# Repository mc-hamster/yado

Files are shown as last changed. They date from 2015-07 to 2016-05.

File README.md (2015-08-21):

# yado (Pronounced Yah-Dew)
"Yet Another Door Opener" ... ESP8266 based Door Controller with JSON REST API and Secure Password ACL. Intened for Garage Doors and Electronic Gate "Buzzers".

## Features

1. Open hardware available in ./hardware
 1. PCB available for purchase at OSHPark
  1. https://www.oshpark.com/shared_projects/0cBHd21f
 2. Full BOM available with distributor list.
  1. (See BOM in ./hardware for part list)
 3. Utilizes nodemcu dev board (It includes many components and just $7 on ebay)
 4. Supports both v0.9 and v1.0 nodemcu footprints. 
   1. http://www.aliexpress.com/wholesale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
1. Open source code available in ./src.
2. Completed Features:
 1. Digest based authentication (No clear text passwords) ... Done
 2. Support for DHCP & Static addresses ... Done
 3. JSON REST API to read door sensors ... Done
 4. Serve all javascript libaries locally ... Done
3. In progress
 1. JSON REST API
  1. Open/Close door ... In progress
  2. Contact Sensor status ... Done
  3. New server digest and payload ... Done
 2. Web Admin Interface for configuration ... In progress
  1. Captive portal ... Done
   1.. Note: DNS server library is unreliable. May cause ESP8266 watchdog reset.

## JSON REST

1. /json/sensors
 1. Return state of the sensors
2. /json/digest/new
 1. Generate a new server digest and associated time

## To build code

1. Install Arduino IDE (It's a horrible environment, but easiest to get going): http://arduino.cc
2. Install board support for the ESP8266: https://github.com/esp8266/Arduino
 1. Select your NodeMCU from the board menu.
3. Install  USB to TTL Bridge Drivers
 1. CH341 : http://www.electrodragon.com/w/CH341 (older nodemcu)
 2. CP2102 : Mac - Drivers built in. Windows - Use windows update. (newer nodemcu)
4. Load the Yagdo code into the Arduino IDE
5. Compile and load the code into your nodemcu dev board.

### Optional

1. Install Atmel Studio and Visual Micro. This is a better IDE than the Arduino IDE.

## Usage: Admin interface

1. Provide power to Yado
2. The LED1 will light solid for a few seconds. During this period, hold down the "user_flash" button.
3. Onces you press the button, LED1 will turn off.
4. When LED2 blinks. Let go of "user_flash".
5. Connect to the Yado access point.
 1. SSID: yado_admin
 2. Password: yado_admin
6. Point your browser to http://192.168.4.1
7. If this is your first time, select the "Load Defaults" link from main menu.

LED2 will continue to blink while Yado is in admin mode. Because unsecured networks are a bad idea, we have conciously decided not to support unsecured Access Points and they won't be listed in the WiFi configuration. Adding support will be a 3 line change, but let's not do it.

Using static IP addresses is recommended, but DHCP also works. The assigned DHCP address is available through the USB serial console (115200, 8n1) on startup, through your home router's interface or you can scan the network for Yado.

Important Note: You will have 30 minutes to make your changes. After 30 minutes, Yado will return to the default operation.

## Usage: Normal Interface

1. Point your web browser to Yado's IP address.
2. Type your access password and click 'open'.

## Usage: Installation

1. Connect the terminal labled "Open1" to your garage door opener.
2. Install an optional door sensor to "Sens1" or "Sens2".

Open2 is not used. Adding support it will some (very) minimal effort, but the UI will need to be kept simple.

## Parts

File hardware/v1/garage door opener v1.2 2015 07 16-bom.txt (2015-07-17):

Partlist exported from /Users/jmcasler/Documents/CloudStation/projects/yado/hardware/garage door opener v2 2015 07 16.sch at 7/17/15 12:47 AM

Part    Value       Device                    Package   Description                MF     MPN         OC_FARNELL OC_NEWARK
C1      10uf        C-USC0603                 C0603     CAPACITOR, American symbol                                        
C2      10uf        C-USC0603                 C0603     CAPACITOR, American symbol                                        
D1      1N4004      DIODE-DO214BA             DO214BA   DIODE                                                             
D2      1N4004      DIODE-DO214BA             DO214BA   DIODE                                                             
D3                  LED0603                   LED-0603  LEDs                                                              
D4                  LED0603                   LED-0603  LEDs                                                              
DS18B20 DS18B20TO92 DS1820TO92                DS1820    DS18B20                                                           
JP1                 PINHD-1X15                1X15      PIN HEADER                                                        
JP2                 PINHD-1X15                1X15      PIN HEADER                                                        
JP3                 PINHD-1X15                1X15      PIN HEADER                                                        
K1      HE3621      HE3621                    HE3621    RELAY                      HAMLIN HE3621A0510 9561943    50F7993  
K2      HE3621      HE3621                    HE3621    RELAY                      HAMLIN HE3621A0510 9561943    50F7993  
OPEN1   1X2-3.5MM   1X2-3.5MM                 1X2-3.5MM 3.5mm Terminal block              OSTTE020161                     
OPEN2   1X2-3.5MM   1X2-3.5MM                 1X2-3.5MM 3.5mm Terminal block              OSTTE020161                     
R1      42          R-US_R0603                R0603     RESISTOR, American symbol                                         
R2      3.3k        R-US_R0603                R0603     RESISTOR, American symbol                                         
R3      42          R-US_R0603                R0603     RESISTOR, American symbol                                         
R4      3.3k        R-US_R0603                R0603     RESISTOR, American symbol                                         
R5      3.3k        R-US_R0603                R0603     RESISTOR, American symbol                                         
R6      3.3k        R-US_R0603                R0603     RESISTOR, American symbol                                         
R7      3.3k        R-US_R0603                R0603     RESISTOR, American symbol                                         
R8      3.3k        R-US_R0603                R0603     RESISTOR, American symbol                                         
R9      3.3k        R-US_R0603                R0603     RESISTOR, American symbol                                         
SENS1   1X2-3.5MM   1X2-3.5MM                 1X2-3.5MM 3.5mm Terminal block              OSTTE020161                     
SENS2   1X2-3.5MM   1X2-3.5MM                 1X2-3.5MM 3.5mm Terminal block              OSTTE020161                     
T1                  MMBT3904LT1-NPN-SOT23-BEC SOT23-BEC NPN Transistror                   MMBT2222A                       
T2                  MMBT3904LT1-NPN-SOT23-BEC SOT23-BEC NPN Transistror                   MMBT2222A

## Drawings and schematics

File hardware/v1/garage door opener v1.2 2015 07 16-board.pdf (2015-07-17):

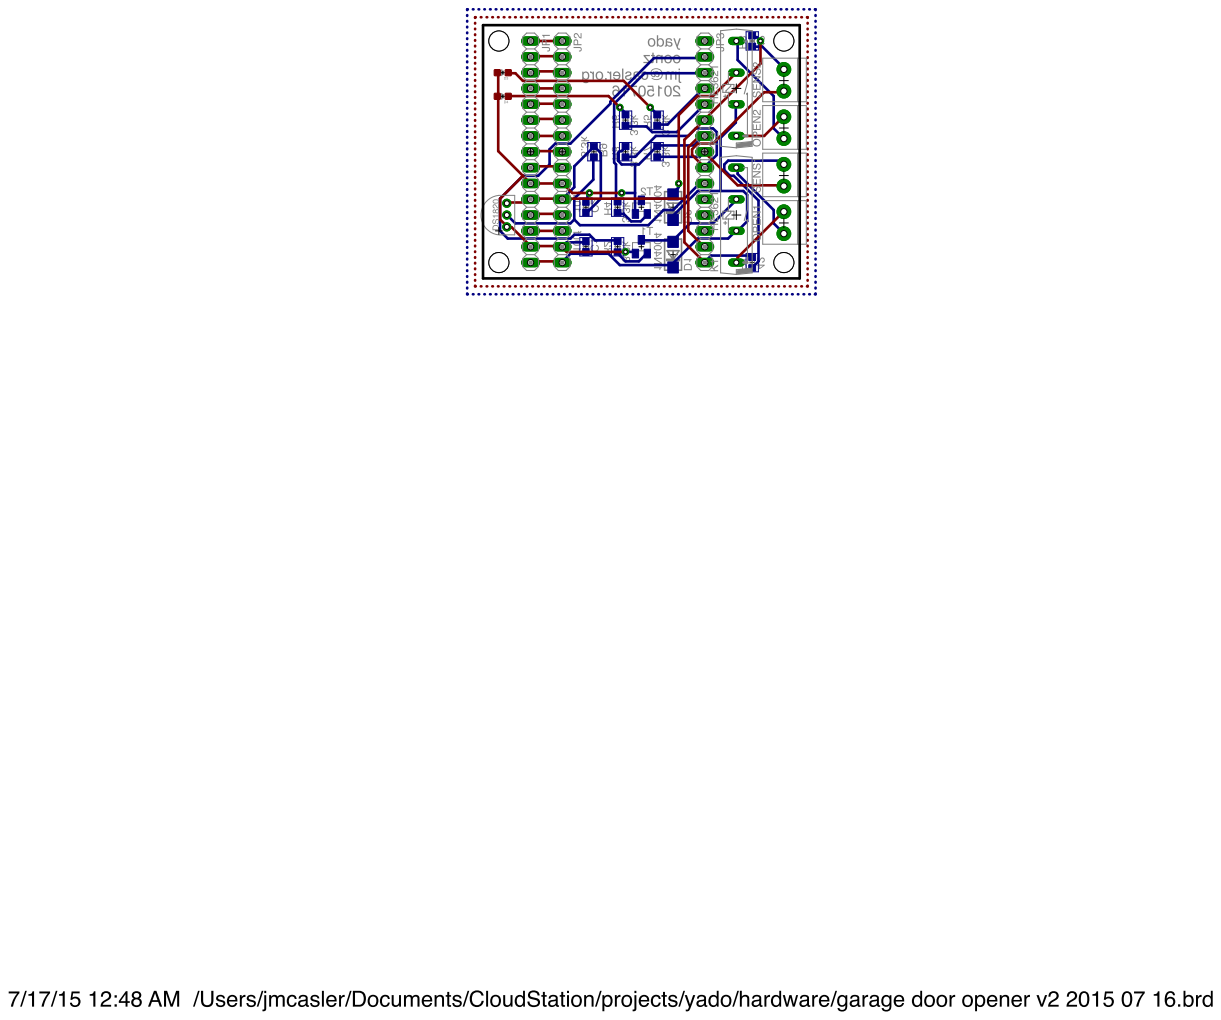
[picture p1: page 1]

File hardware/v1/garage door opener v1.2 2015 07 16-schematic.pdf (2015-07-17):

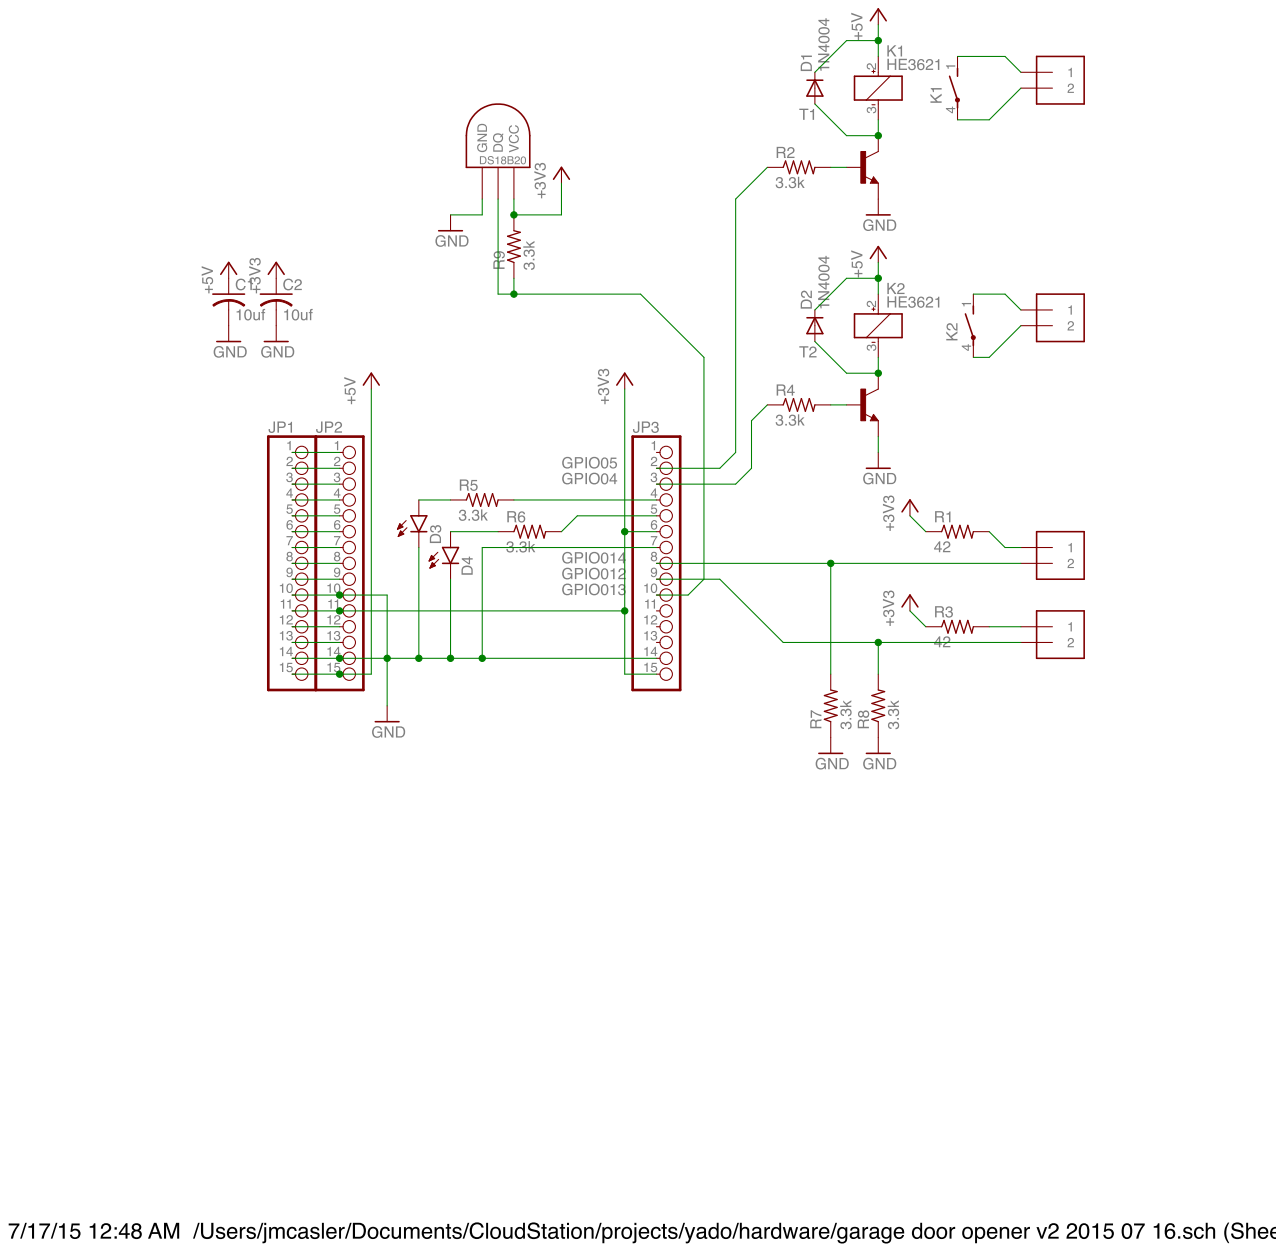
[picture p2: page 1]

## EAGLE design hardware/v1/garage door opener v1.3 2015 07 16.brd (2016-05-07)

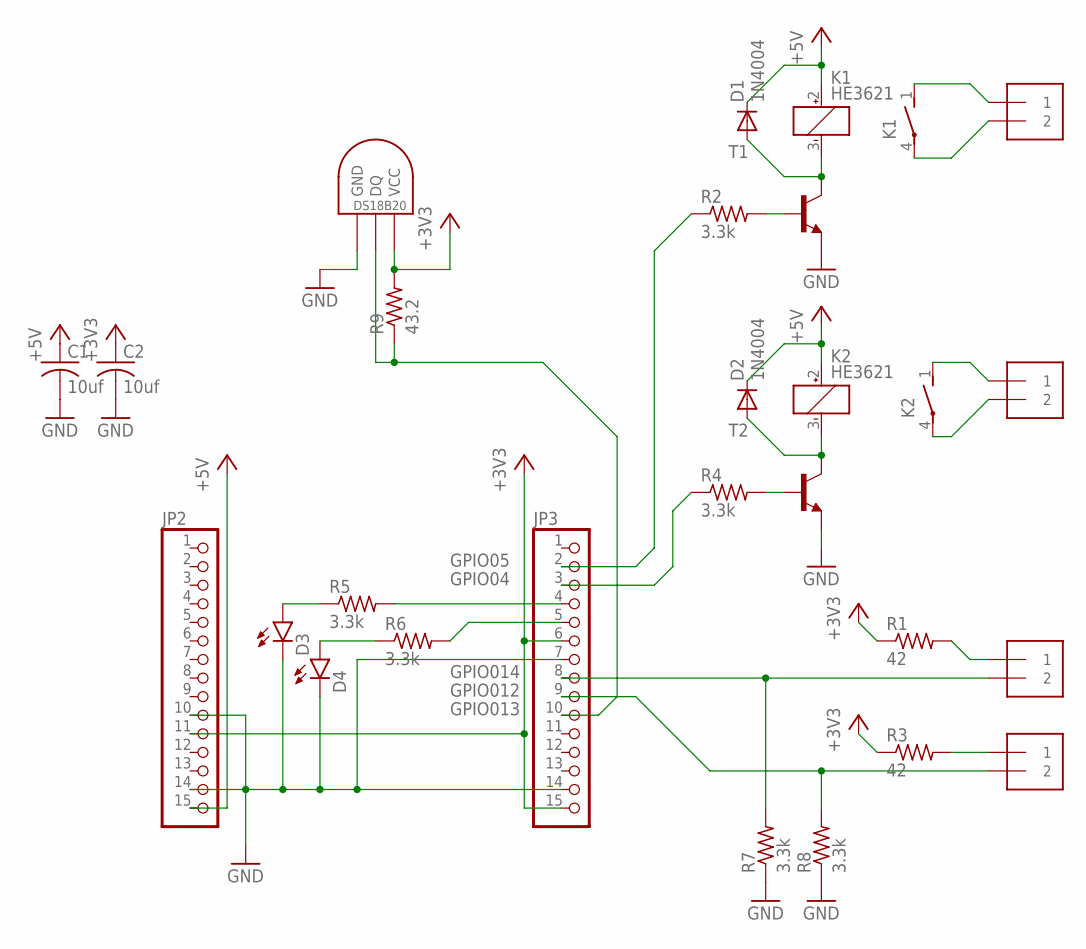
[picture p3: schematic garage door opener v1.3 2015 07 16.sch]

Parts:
C1, C2: 10uf; C0603
D1, D2: 1N4004; DO214BA
D3, D4: LED0603; LED-0603
DS18B20: DS18B20TO92; DS1820
JP2, JP3: PINHD-1X15; 1X15
K1, K2: HE3621; MPN HE3621A0510
OPEN1, OPEN2: 1X2-3.5MM; MPN OSTTE020161
R1, R3: 42; R0603
R2, R4, R5, R6, R7, R8: 3.3k; R0603
R9: 43.2; R0603
SENS1, SENS2: 1X2-3.5MM; MPN OSTTE020161
T1, T2: MMBT3904LT1-NPN-SOT23-BEC; SOT23-BEC; MPN MMBT2222A

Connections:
+3V3: C2.1, DS18B20.VDD (VCC), JP2.11, JP3.6, JP3.15, R1.1, R3.1, R9.2
+5V: C1.1, D1.C, D2.C, JP2.15, K1.2 (+), K2.2 (+)
GND: C1.2, C2.2, D3.C, D4.C, DS18B20.GND, JP2.10, JP2.14, JP3.7, JP3.14, R7.1, R8.1, T1.E, T2.E
unnamed: K1.1 (S), OPEN1.1
unnamed: K1.4, OPEN1.2
unnamed: JP3.8, R7.2, SENS1.2
unnamed: R1.2, SENS1.1
unnamed: D1.A, K1.3 (-), T1.C
unnamed: JP3.2, R2.1
unnamed: R2.2, T1.B
unnamed: JP3.4, R5.2
unnamed: JP3.5, R6.2
unnamed: R3.2, SENS2.1
unnamed: JP3.9, R8.2, SENS2.2
unnamed: K2.1 (S), OPEN2.1
unnamed: K2.4, OPEN2.2
unnamed: D2.A, K2.3 (-), T2.C
unnamed: JP3.3, R4.1
unnamed: R4.2, T2.B
unnamed: D4.A, R6.1
unnamed: D3.A, R5.1
unnamed: DS18B20.DQ, JP3.10, R9.1

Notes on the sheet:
GPIO05
GPIO04
GPIO014
GPIO012
GPIO013

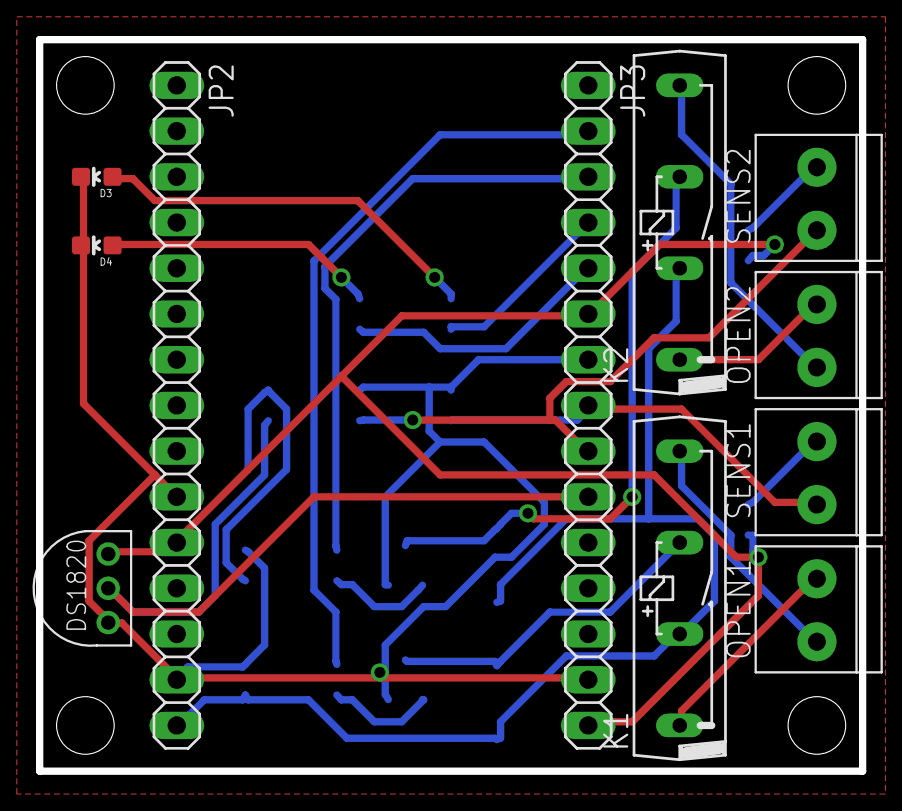
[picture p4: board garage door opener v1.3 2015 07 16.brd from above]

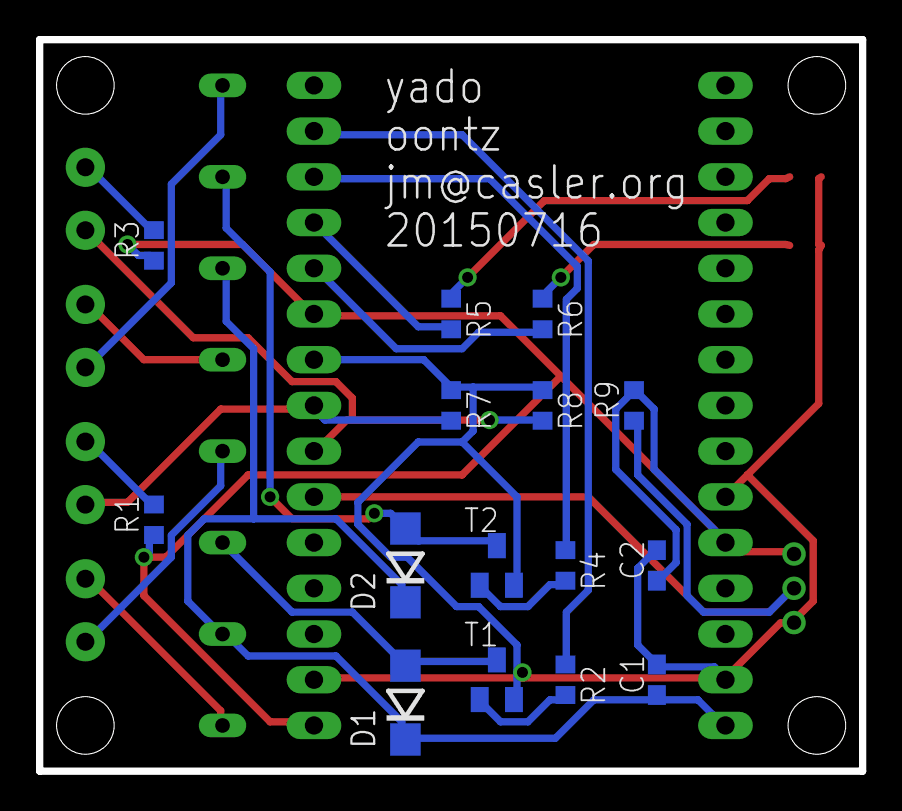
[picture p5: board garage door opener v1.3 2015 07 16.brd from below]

Board: 2 copper layers, 45.7 x 40.6 mm, 26 parts (15 on the bottom side), 22 nets.

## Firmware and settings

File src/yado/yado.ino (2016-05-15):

/*
 * Copyright (c) 2015-2016, Jm Casler
 * All rights reserved.
 *
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
 * * Neither the name of Jm Casler nor the names of its
 *   contributors may be used to endorse or promote products derived from
 *   this software without specific prior written permission.
 *
 * THIS SOFTWARE IS PROVIDED BY THE COPYRIGHT HOLDERS AND CONTRIBUTORS "AS IS" AND
 * ANY EXPRESS OR IMPLIED WARRANTIES, INCLUDING, BUT NOT LIMITED TO, THE IMPLIED
 * WARRANTIES OF MERCHANTABILITY AND FITNESS FOR A PARTICULAR PURPOSE ARE
 * DISCLAIMED. IN NO EVENT SHALL THE COPYRIGHT HOLDER OR CONTRIBUTORS BE LIABLE FOR
 * ANY DIRECT, INDIRECT, INCIDENTAL, SPECIAL, EXEMPLARY, OR CONSEQUENTIAL DAMAGES
 * (INCLUDING, BUT NOT LIMITED TO, PROCUREMENT OF SUBSTITUTE GOODS OR SERVICES;
 * LOSS OF USE, DATA, OR PROFITS; OR BUSINESS INTERRUPTION) HOWEVER CAUSED AND ON
 * ANY THEORY OF LIABILITY, WHETHER IN CONTRACT, STRICT LIABILITY, OR TORT
 * (INCLUDING NEGLIGENCE OR OTHERWISE) ARISING IN ANY WAY OUT OF THE USE OF THIS
 * SOFTWARE, EVEN IF ADVISED OF THE POSSIBILITY OF SUCH DAMAGE.
 */

#include <ESP8266WiFi.h>
#include <DNSServer.h>
#include <WiFiClient.h>
#include <ESP8266WebServer.h>
#include <Hash.h>

#include <EEPROM.h>
#include "EEPROMAnything.h"

#include <ESP8266HTTPUpdateServer.h>
#include <ESP8266mDNS.h>


// Configuration Start
const uint8_t numberOfUsers = 5;
const uint8_t passwordLength = 16;
const uint8_t noteLength = 32;

const uint8_t sensorLabelLength = 16;

const char* host = "yado";

// Contact sensors
struct sensor_t
{
  boolean enabled;
  boolean invert;
  char name[sensorLabelLength + 1]; // One more byte than required; String needs to be null terminated
  char high[sensorLabelLength + 1];  // One more byte than required; String needs to be null terminated
  char low[sensorLabelLength + 1];  // One more byte than required; String needs to be null terminated
};

struct temperature_t
{
  boolean enabled;
  boolean metricImperial; // 0 = Metric, 1 = Imperial
};

//
struct access_t
{
  uint8_t admin;  // Reserved
  uint8_t conf;   // Reserved
  char password[passwordLength + 1]; // One more byte than required; String needs to be null terminated
  char user[passwordLength + 1];  // Not yet used.
  char note[noteLength + 1];  // One more byte than required; String needs to be null terminated
};

// This structure should not grow larger than 1024 bytes.
struct settings_t
{
  uint8_t initialized;       // If not "1", then we have not yet initialized with defaults
  char ssid[33];         // One more byte than required; String needs to be null terminated
  char ssidPassword[65]; // One more byte than required; String needs to be null terminated
  uint8_t ipMode; // 0 = Dynamic, 1 = Static
  uint8_t ipAddress[4]; // 255.255.255.255
  uint8_t ipGateway[4]; // 255.255.255.255
  uint8_t ipSubnet[4];  // 255.255.255.255
  access_t accessGeneral[numberOfUsers];
  sensor_t contactSensor[2];
  temperature_t temperature;
} settings;

int requestTTL = 120;


// Configuration End

const byte DNS_PORT = 53;
ESP8266WebServer httpServer ( 80 );
ESP8266HTTPUpdateServer httpUpdater;
DNSServer dnsServer;

// Pin Assignment
const int ledHTTP = 0;     // Toggled on HTTP Status
const int ledCONNECTED = 2; // Toggled on when AP connected
const int sensor1 = 14;
const int sensor2 = 12;
const int open1 = 5;
const int open2 = 4;

// These buttons are exposed on the nodemcu dev board
const int key_user = 16; // What can we do with this button?
const int key_flash = 0; // If pressed within 5 seconds of power on, enter admin mode
// End Pin Assignment

unsigned long secretRandNumber; // We will generate a new secret on startup.

int lastAccessTime = 0;

String inputString = "";         // a string to hold incoming data

boolean deviceAdmin = 0;

// Define the LED state for ledHTTP
//   This is used for blinking the LED with a non-blocking method
boolean ledHTTPState = LOW;
unsigned long    ledHTTPStateMills = 0;
long    ledHTTPStateInterval = 250; // How fast to blink the LED



void setup ( void ) {
  EEPROM.begin(1024); // 512 bytes should be more than enough (famous last words)
  loadSettings();

  // TODO: Move this into the admin setup menu.
  settings.contactSensor[0].enabled = 1; // Manually enable this for now.
  settings.contactSensor[0].invert = 9; // Manually enable this for now.


  inputString.reserve(50);

  // Set relays as outputs;
  pinMode ( open1, OUTPUT );
  pinMode ( open2, OUTPUT );
  digitalWrite ( open1, 0 );
  digitalWrite ( open2, 0 );


  //  There is a bug in the esp8266 library which prevents the pulldown from functioning
  //    https://github.com/esp8266/Arduino/issues/478
  pinMode ( sensor1, INPUT );
  pinMode ( sensor2, INPUT );

  // Set status LEDs to OUTPUT
  pinMode ( ledHTTP, OUTPUT );
  pinMode ( ledCONNECTED, OUTPUT );
  digitalWrite ( ledHTTP, 0 );
  digitalWrite ( ledCONNECTED, 0 );

  // Get access to the key_user button
  pinMode( key_flash, INPUT_PULLUP );


  delay(5000);
  // Set deviceAdmin to one if key_flash is depressed. Otherwise, use defaults.
  if (digitalRead( key_flash ) == 0) {
    deviceAdmin = 1;
    pinMode( key_flash, OUTPUT );
  } else {
    pinMode( key_flash, OUTPUT );
  }

  Serial.begin ( 115200 );

  if (deviceAdmin) {
    WiFi.mode(WIFI_AP);
    WiFi.softAP("yado_admin", "yado_admin");
    //WiFi.mode(WIFI_AP);
    WiFi.config ( IPAddress(192, 168, 4, 1), IPAddress(192, 168, 4, 1), IPAddress(255, 255, 255, 0)) ;
    delay(10);

    // if DNSServer is started with "*" for domain name, it will reply with
    // provided IP to all DNS request
    dnsServer.start(DNS_PORT, "*", IPAddress(192, 168, 4, 1));

    //WiFi.printDiag(Serial);
    Serial.println ( "Entering admin mode." );

    Serial.print ( "IP address: " );
    Serial.println ( WiFi.softAPIP() );
    printAPMacAddress();


    if ( MDNS.begin ( host ) ) {
      Serial.println ( "MDNS responder started" );
    } else {
      Serial.println ( "MDNS responder NOT started" );
    }

    // We are using the amount of time required to connect to the AP as the seed to a random number generator.
    //   We should look for other ways to improve the seed. This should be "good enough" for now.

    httpServer.on ( "/", handleAdminFrameset );
    httpServer.on ( "/leftnav", handleAdminNav );
    httpServer.on ( "/conf/wifi", handleAdminConfWifi );
    httpServer.on ( "/conf/network", handleAdminConfNetwork );
    httpServer.on ( "/conf/accounts", handleAdminConfAccounts );
    httpServer.on ( "/conf/sensors", handleAdminConfSensors );
    httpServer.on ( "/system/defaults", handleAdminDefaults );
    httpServer.on ( "/system/settings", handleAdminSettings );
    httpServer.on ( "/system/restart", handleAdminRestart);
    httpServer.on ( "/system/apply", handleAdminApply);
    httpServer.on ( "/yado.css", handleCSS);

    httpServer.onNotFound ( handleNotFound );

    httpUpdater.setup(&httpServer); // Handle OTA Updates. Go to http://yado.local/update

    httpServer.begin();
    Serial.println ( "HTTP server started" );

    MDNS.addService("http", "tcp", 80);
    Serial.printf("HTTPServer ready! Open http://%s.local in your browser\n", host);
    Serial.printf("HTTPUpdateServer ready! Open http://%s.local/update in your browser\n", host);


  } else {
    WiFi.begin ( settings.ssid, settings.ssidPassword );
    WiFi.mode ( WIFI_STA );



    // Documentation says this is supposed to come before WiFi.begin, but when it is there -- it doesn't work. WHY?!?!?!
    if (settings.ipMode == 1) { // 0 = Dynamic, 1 = Static
      WiFi.config ( settings.ipAddress, settings.ipGateway, settings.ipSubnet) ;
    }

    Serial.println ( "" );

    //EEPROM_readAnything(0, settings);

    // Wait for connection
    while ( WiFi.status() != WL_CONNECTED ) {
      delay ( 500 );
      Serial.print ( "." );
    }

    digitalWrite ( ledCONNECTED, 1 );

    WiFi.printDiag(Serial);

    Serial.print ( "IP address: " );
    Serial.println ( WiFi.localIP() );
    printMacAddress();

    if ( MDNS.begin ( host ) ) {
      Serial.println ( "MDNS responder started" );
    } else {
      Serial.println ( "MDNS responder NOT started" );
    }

    // We are using the amount of time required to connect to the AP as the seed to a random number generator.
    //   We should look for other ways to improve the seed. This should be "good enough" for now.
    randomSeed(micros());
    secretRandNumber = random(2147483646); // Full range of long 2147483647
    Serial.println("Secret: " + String(secretRandNumber));

    httpServer.on ( "/", handleRoot );
    httpServer.on ( "/externalScript.js", handleExternalScriptJS );
    httpServer.on ( "/json/sensors", handleJSONSensors );
    httpServer.on ( "/json/digest/new", handleJSONDigestNew );
    httpServer.on ( "/yado.css", handleCSS);

    httpServer.onNotFound ( handleNotFound );
    httpServer.begin();
    Serial.println ( "HTTP server started" );

    MDNS.addService("http", "tcp", 80);
    Serial.printf("HTTP Server ready! Open http://%s.local in your browser\n", host);

  
  }

}


void loop ( void ) {

  httpServer.handleClient();
  dnsServer.processNextRequest();

  if (deviceAdmin) {
    unsigned long ledHTTPCurrentMills = millis();

    if (ledHTTPCurrentMills - ledHTTPStateMills > ledHTTPStateInterval) {
      ledHTTPStateMills = ledHTTPCurrentMills;

      if (ledHTTPState) {
        ledHTTPState = 0;
      } else {
        ledHTTPState = 1;
      }
      digitalWrite( ledCONNECTED, ledHTTPState );
      //Serial.println ( WiFi.softAPIP() );
    }

    // If we've been in admin mode for 30 minutes, reboot ESP to get out of
    //   admin mode.
    if (millis() > 1800000) {
      ESP.reset();
    }
  }

}

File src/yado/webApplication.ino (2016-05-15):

void handleExternalScriptJS() {
  digitalWrite ( ledHTTP, 1 );


  String externJavascriptString = "\n"
                                  "/*CryptoJS v3.1.2\n"
                                  "code.google.com/p/crypto-js\n"
                                  "(c) 2009-2013 by Jeff Mott. All rights reserved.\n"
                                  "code.google.com/p/crypto-js/wiki/License\n"
                                  "*/\n"
                                  "var CryptoJS=CryptoJS||function(e,m){var p={},j=p.lib={},l=function(){},f=j.Base={extend:function(a){l.prototype=this;var c=new l;a&&c.mixIn(a);c.hasOwnProperty(\"init\")||(c.init=function(){c.$super.init.apply(this,arguments)});c.init.prototype=c;c.$super=this;return c},create:function(){var a=this.extend();a.init.apply(a,arguments);return a},init:function(){},mixIn:function(a){for(var c in a)a.hasOwnProperty(c)&&(this[c]=a[c]);a.hasOwnProperty(\"toString\")&&(this.toString=a.toString)},clone:function(){return this.init.prototype.extend(this)}},\n"
                                  "n=j.WordArray=f.extend({init:function(a,c){a=this.words=a||[];this.sigBytes=c!=m?c:4*a.length},toString:function(a){return(a||h).stringify(this)},concat:function(a){var c=this.words,q=a.words,d=this.sigBytes;a=a.sigBytes;this.clamp();if(d%4)for(var b=0;b<a;b++)c[d+b>>>2]|=(q[b>>>2]>>>24-8*(b%4)&255)<<24-8*((d+b)%4);else if(65535<q.length)for(b=0;b<a;b+=4)c[d+b>>>2]=q[b>>>2];else c.push.apply(c,q);this.sigBytes+=a;return this},clamp:function(){var a=this.words,c=this.sigBytes;a[c>>>2]&=4294967295<<\n"
                                  "32-8*(c%4);a.length=e.ceil(c/4)},clone:function(){var a=f.clone.call(this);a.words=this.words.slice(0);return a},random:function(a){for(var c=[],b=0;b<a;b+=4)c.push(4294967296*e.random()|0);return new n.init(c,a)}}),b=p.enc={},h=b.Hex={stringify:function(a){var c=a.words;a=a.sigBytes;for(var b=[],d=0;d<a;d++){var f=c[d>>>2]>>>24-8*(d%4)&255;b.push((f>>>4).toString(16));b.push((f&15).toString(16))}return b.join(\"\")},parse:function(a){for(var c=a.length,b=[],d=0;d<c;d+=2)b[d>>>3]|=parseInt(a.substr(d,\n"
                                  "2),16)<<24-4*(d%8);return new n.init(b,c/2)}},g=b.Latin1={stringify:function(a){var c=a.words;a=a.sigBytes;for(var b=[],d=0;d<a;d++)b.push(String.fromCharCode(c[d>>>2]>>>24-8*(d%4)&255));return b.join(\"\")},parse:function(a){for(var c=a.length,b=[],d=0;d<c;d++)b[d>>>2]|=(a.charCodeAt(d)&255)<<24-8*(d%4);return new n.init(b,c)}},r=b.Utf8={stringify:function(a){try{return decodeURIComponent(escape(g.stringify(a)))}catch(c){throw Error(\"Malformed UTF-8 data\");}},parse:function(a){return g.parse(unescape(encodeURIComponent(a)))}},\n"
                                  "k=j.BufferedBlockAlgorithm=f.extend({reset:function(){this._data=new n.init;this._nDataBytes=0},_append:function(a){\"string\"==typeof a&&(a=r.parse(a));this._data.concat(a);this._nDataBytes+=a.sigBytes},_process:function(a){var c=this._data,b=c.words,d=c.sigBytes,f=this.blockSize,h=d/(4*f),h=a?e.ceil(h):e.max((h|0)-this._minBufferSize,0);a=h*f;d=e.min(4*a,d);if(a){for(var g=0;g<a;g+=f)this._doProcessBlock(b,g);g=b.splice(0,a);c.sigBytes-=d}return new n.init(g,d)},clone:function(){var a=f.clone.call(this);\n"
                                  "a._data=this._data.clone();return a},_minBufferSize:0});j.Hasher=k.extend({cfg:f.extend(),init:function(a){this.cfg=this.cfg.extend(a);this.reset()},reset:function(){k.reset.call(this);this._doReset()},update:function(a){this._append(a);this._process();return this},finalize:function(a){a&&this._append(a);return this._doFinalize()},blockSize:16,_createHelper:function(a){return function(c,b){return(new a.init(b)).finalize(c)}},_createHmacHelper:function(a){return function(b,f){return(new s.HMAC.init(a,\n"
                                  "f)).finalize(b)}}});var s=p.algo={};return p}(Math);\n"
                                  "(function(){var e=CryptoJS,m=e.lib,p=m.WordArray,j=m.Hasher,l=[],m=e.algo.SHA1=j.extend({_doReset:function(){this._hash=new p.init([1732584193,4023233417,2562383102,271733878,3285377520])},_doProcessBlock:function(f,n){for(var b=this._hash.words,h=b[0],g=b[1],e=b[2],k=b[3],j=b[4],a=0;80>a;a++){if(16>a)l[a]=f[n+a]|0;else{var c=l[a-3]^l[a-8]^l[a-14]^l[a-16];l[a]=c<<1|c>>>31}c=(h<<5|h>>>27)+j+l[a];c=20>a?c+((g&e|~g&k)+1518500249):40>a?c+((g^e^k)+1859775393):60>a?c+((g&e|g&k|e&k)-1894007588):c+((g^e^\n"
                                  "k)-899497514);j=k;k=e;e=g<<30|g>>>2;g=h;h=c}b[0]=b[0]+h|0;b[1]=b[1]+g|0;b[2]=b[2]+e|0;b[3]=b[3]+k|0;b[4]=b[4]+j|0},_doFinalize:function(){var f=this._data,e=f.words,b=8*this._nDataBytes,h=8*f.sigBytes;e[h>>>5]|=128<<24-h%32;e[(h+64>>>9<<4)+14]=Math.floor(b/4294967296);e[(h+64>>>9<<4)+15]=b;f.sigBytes=4*e.length;this._process();return this._hash},clone:function(){var e=j.clone.call(this);e._hash=this._hash.clone();return e}});e.SHA1=j._createHelper(m);e.HmacSHA1=j._createHmacHelper(m)})();";



  if (0) {
    // TODO: If we recieve a If-None-Match header and it matches the Etag we defined, then
    //       return a  HTTP 304 Not Modified header with no content.
    //       -- See: http://en.wikipedia.org/wiki/HTTP_ETag for protocol details
  } else {


    // Define header to encourage browsers to cache this page.
    httpServer.sendHeader ( "ETag", "CacheThisForever", 0 );
    httpServer.sendHeader ( "Expires", "Mon, 08 Jun 2035 00:19:36 GMT", 0 );
    httpServer.sendHeader ( "Cache-Control", "public, max-age=31536000", 0 ); // 31536000 = 1 year
    httpServer.send ( 200, "text/plain", externJavascriptString );
  }

  digitalWrite ( ledHTTP, 0 );
}

void handleJSONSensors () {
  digitalWrite ( ledHTTP, 1 );

  String message = "";
  message += "{\n";
  message += "  \"data\" : {\n";
  message += "    \"sensor1\" : " + String(digitalRead(sensor1)) + ",\n";
  message += "    \"sensor2\" : " + String(digitalRead(sensor2)) + "\n";
  message += "  }\n";
  message += "}\n";

  httpServer.send ( 200, "application/json", message );

  digitalWrite ( ledHTTP, 0 );
}

void handleJSONDigestNew () {
  digitalWrite ( ledHTTP, 1 );

  int sec = millis() / 1000; // TODO: Revert to the previous line. This is here for debugging.
  char digestStringHex[41];

  computeServerDigest(sec, digestStringHex);

  String message = "";
  message += "{\n";
  message += "  \"data\" : {\n";
  message += "    \"sec\" : " + String(sec) + ",\n";
  message += "    \"digest\" : \"" + String(digestStringHex) + "\"\n";
  message += "  }\n";
  message += "}\n";

  httpServer.send ( 200, "application/json", message );

  digitalWrite ( ledHTTP, 0 );
}
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

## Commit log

2015-06-18 Initial check in of Eagle files.
    [garage door opener.brd, garage door opener.sch]
2015-06-18 Updated with BOM
    [garage door opener.brd, garage door opener.sch]
2015-06-19 Updated with pull down resistor for sense inputs.
    [garage door opener.brd, garage door opener.sch]
2015-06-23 Lots of refactoring
    [garage door opener.sch]
2015-06-27 Removed trough hole diode, removed top silkscreen, rerouted.
    [garage door opener.brd, garage door opener.sch]
2015-06-27 removed through hole diode
    [garage door opener.brd]
2015-06-27 Removed power pads from left (not really needed?). Replaced LEDs with a proper LED footprint. Moved capacitors closer to headers.
    [garage door opener.brd]
2015-06-27 removed power header. swapped footprint for led.
    [garage door opener.sch]
2015-06-28 Set sensor inputs to INPUT rather than INPUT_PULLDOWN. Print MAC address to USB on boot.
2015-07-01 Switched from triggering watchdog to calling the ESP.reset() method.
2015-07-01 No longer using INPUT_PULLDOWN. While it's in the SDK, it's not implemented by the silicon.
    [yado.ino]
2015-07-04 Changed the mime type of json responses. Added error feedback to web browser.
    [webApplication.ino]
2015-07-04 Refactored reading the sensors to return human readable strings.
2015-07-04 fixed rest response. forgot to quote the string. also added ability to invert the response from the door sensors. this is to support both NC and NO type contacts.
    [webApplication.ino, webUtilities.ino]
2015-07-06 Updated with footprint for ds18b20 ... why? feature creep!
    [garage door opener.brd, garage door opener.sch]
2015-07-13 Fixed static / dynamic ip selection
    [yado.ino]
2015-07-13 esp8266WebServer has a limit on file size for response content of ~2.5k. Started using the client method of the server to handle the response directly. Now can serve ~25k without much issue.
    [webApplication.ino, yado.ino]
2015-07-17 Support for an admin mode to make config changes - After power on, LED1 will light for 5 seconds. During this period, hold down the user_flash button. LED2 will start to blink. Release the button onc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
2015-07-17 If we've been in admin mode for 30 minutes, reboot to get out of admin mode.
    [yado.ino]
2015-07-17 Updated PCB. Removed power test points on left. Moved most surface mount components onto the back of the board. Switched to using just two resistor values (easier to source components).
    [garage door opener v2 2015 07 16.brd, garage door opener v2 2015 07 16.sch]
2015-07-17 BOM and PDF of schematic / board.
2015-07-17 Updated with admin pages that scans for wifi ap and prints settings.
2015-07-19 Added data structure to store configuration on contact sensors.
2015-07-19 Deleting files, these will be moved to a new location
    [garage door opener v2 2015 07 16.brd, garage door opener v2 2015 07 16.sch, garage door opener.brd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]
2015-07-19 Moved to v1 folder.
    [garage door opener v1.3 2015 07 16.brd, garage door opener v1.3 2015 07 16.sch]
2015-08-06 Added frameset for admin mode. Add display of basic flash statistics.
2015-08-06 Added support for frameset.
2015-08-21 defaults - Automatically load defaults on initial start up. Change default IP address & gateway. serialMenu - Deprecated serialMenu. This should not be needed. It's easier to use the web interface. w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
2016-05-07 Updated to support the new ESP8266 v2.0.0 Arduino Library.
2016-05-07 Changed value of DS18B20 pull up resistor. Change is insignificant and the old part will continue to work.
    [garage door opener v1.3 2015 07 16.brd, garage door opener v1.3 2015 07 16.sch]
2016-05-11 Google has stopped hosting the CryptoJS library. The original developer (Jeff Mott) no longer supports it on Google Code. Yado updated to a locally served version.
    [webApplication.ino, yado.ino]
2016-05-15 removed sendMime function and replaced it with the httpserver.send function. esp8266webserver library now performs as expected.
    [webApplication.ino, webUtilities.ino]

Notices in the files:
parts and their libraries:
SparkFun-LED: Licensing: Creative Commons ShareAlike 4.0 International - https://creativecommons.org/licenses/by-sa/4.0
